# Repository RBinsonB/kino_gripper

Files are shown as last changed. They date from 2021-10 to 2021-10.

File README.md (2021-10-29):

# Kino Gripper
3D printed Kino gripper repository/ROS package.

Kino, from the greek κίνημα kinema ("movement, motion"), is an adaptative gripper using a [Dynamixel AX-12A servomotor](https://emanual.robotis.com/docs/en/dxl/ax/ax-12a/) as actuator. It leverages the abilies of the smart servomotor: compliance, possibility to set torque, velocity... Communication with the servomotor is handled with an integrated [USB2AX](http://www.xevelabs.com/doku.php?id=product:usb2ax:usb2ax). Power is provided by a DC-DC buck converter.

The gripper is designed to be mounted on a [HEBI Robotics Arm](https://www.hebirobotics.com/robot-arms) but can easily be modified to be mounted on other arms.

[Assembly instructions can be found here](/resources/documentation/kino_gripper_assembly.md).

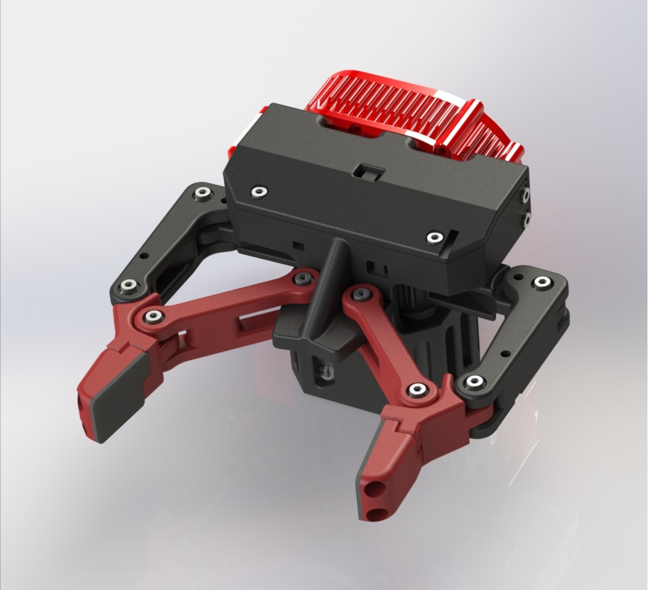
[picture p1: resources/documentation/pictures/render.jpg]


## Features

### Gripper mount
The gripper is designed to be mounted on a HEBI Robotics arm.



Screw the base attachement part to the output shaft of the HEBI actuator.



Connect with the main part of the gripper.



Slide the main part of the gripper, being careful not to damage the USB connector. Screw the main part in place

### Compliance
Torque and position compliance is provided by the servomotor. The compliance values can be set according to the [Dynamixel AX-12A documentation](https://emanual.robotis.com/docs/en/dxl/ax/ax-12a/#compliance-margin-26-27).

### Adaptive grip
Thanks to the spring on each finger, the gripper can fold to encircle small objects. The spring can be changed to allow for easier/harder finger deformation.

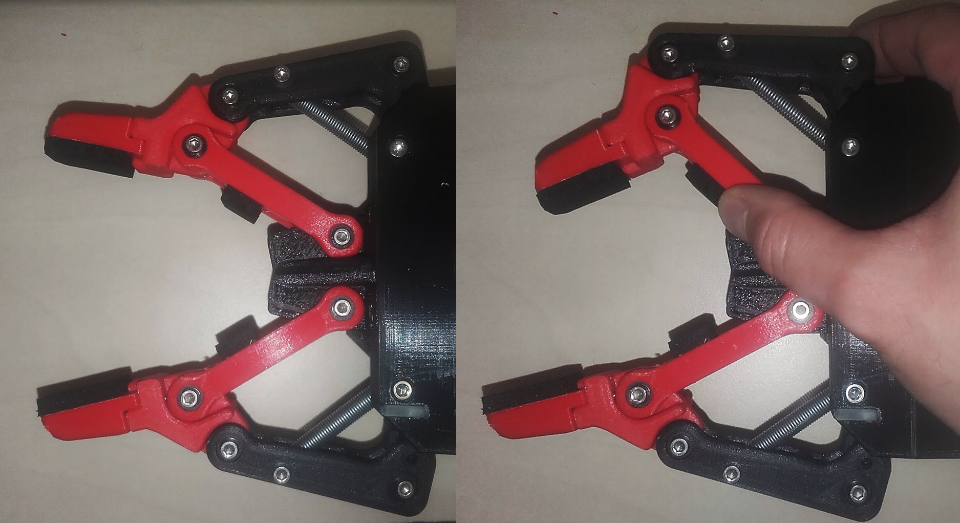
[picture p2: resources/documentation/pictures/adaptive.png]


### Changeable finger tips
Finger tips can be change by simply unscrewing/screwing.

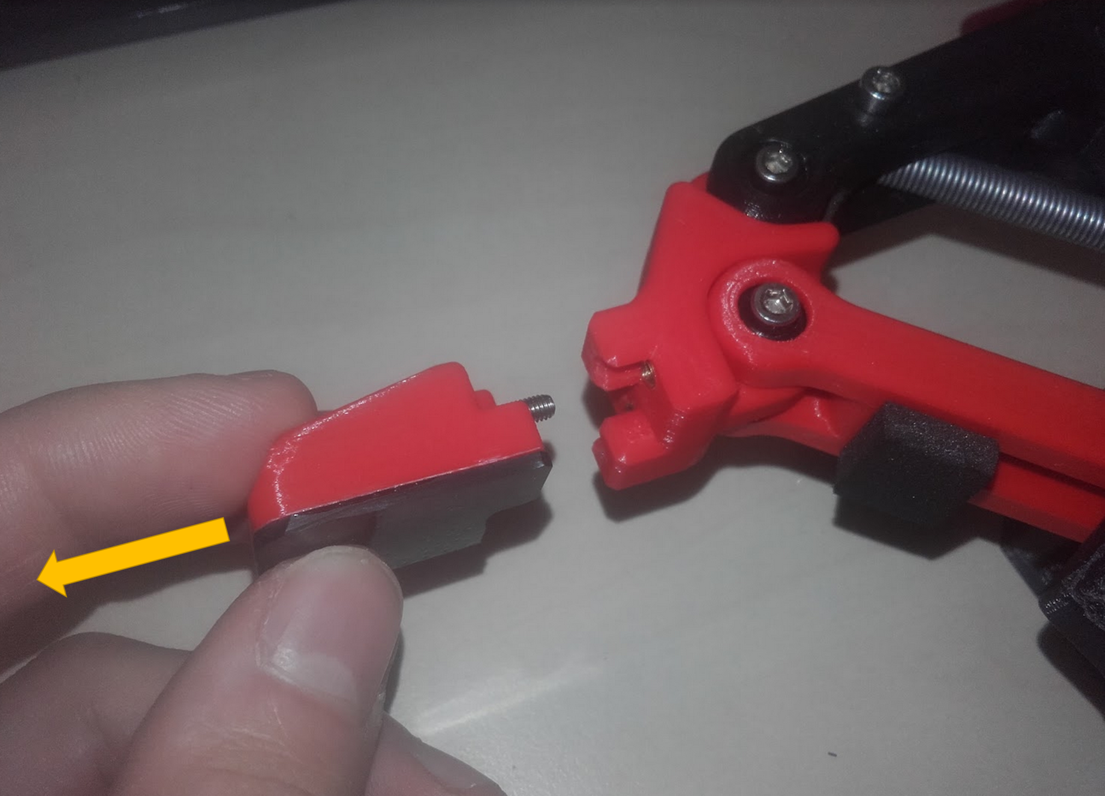
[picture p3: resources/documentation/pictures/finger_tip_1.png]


Three finger tip types are provided, but more can easily be designed:
* Default, with zig-zag pattern
* Thin pads, to be printed and completed by gluing a thin rubber pad
* Thick pads, to be printed and completed by gluing a thick foam pad

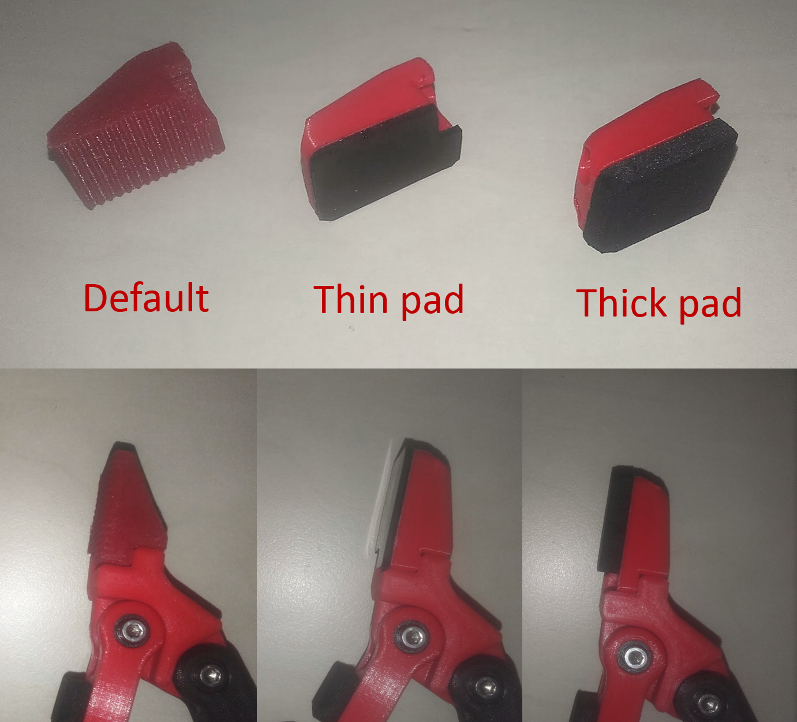
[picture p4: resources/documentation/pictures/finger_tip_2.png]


## Installation
The gripper package can be used as a ROS or C++ package.

### Dependencies
- [Robot Operating System (ROS)](http://wiki.ros.org)
- [Dynamixel SDK](https://emanual.robotis.com/docs/en/software/dynamixel/dynamixel_sdk/download/). Either through ROS package or direct install.

### Building
To build the package, clone the current repository in your catkin workspace and build it.
```
cd catkin_ws/src
git clone https://github.com/RBinsonB/kino_gripper.git
```
Build your workspace with either *catkin_make* or *catkin build*
```
cd ...
catkin_make
```

## Usage
### ROS Node
The gripper ROS node can be launched using the following command. Don't forget to set the appropriate port, device ID and baudrate parameters beforehand.
```
rosrun kino_gripper kino_gripper_node
```

#### Subscribed Topics
- `gripper_cmd` ([control_msgs/GripperCommand](http://docs.ros.org/en/melodic/api/control_msgs/html/msg/GripperCommand.html))

    Gripper command message. The position field is commanded distance between the fingers. Torque command is not taken into account and the default servomotor torque will be used.

#### Parameters
- `~port` (string, default: "/dev/ttyACM0")

    Servomotor port. For more information check about USB2AX and AX-12A Dynamixel servomotor.
    
- `~baudrate` (int, default: 1000000)

    Servomotor baudrate in bps. For more information check about USB2AX and AX-12A Dynamixel servomotor.
    
- `~device_id` (uint8_t, default: 1)

    Servomotor ID. For more information check about AX-12A Dynamixel servomotor.
    
### C++
The gripper library can be used independently of ROS. To do so, include the appropriate header in your file.
```cpp
#include <kino_gripper.h>

```

To use the gripper, you can create a gripper object using:
```cpp
KinoGripper(int device_id, char const* device_name, int baudrate)
```
The gripper can then be closed or opened using the Close() and Open() functions.
Example:
```cpp
KinoGripper gripper(1, "/dev/ttyACM0", 1000000);

gripper.Close(40.0);              // Close fingers to 40mm
while (!gripper.IsClosed()){ };   // Wait for gripper to finish
gripper.Close(0.0);               // Close fingers to 0mm
while (!gripper.IsClosed()){ };
gripper.Open();                   // Open gripper completely
while (!gripper.IsClosed()){ };
```

#### API
##### Public Member Functions
```cpp
KinoGripper(int device_id, char const* device_name, int baudrate)
  Gripper object constructor.
  Parameters : 
      device_id Dynamixel servomotor device ID
      device_name Dynamixel servomotor port
      baudrate Dynamixel servomotor baudrate in bps
```
```cpp
void InitGripper()
  Initializes the gripper servomotor and build lookup table for position command
```
```cpp
bool Close(float distance)
  Close the gripper to the given distance (between fingers)
  Parameters : 
      distance Distance between fingers in mm
  Returns :
      True if command sent successfully to servomotor
```
```cpp
bool Open()
  Open the gripper fully by sending maximum angle command (can be set SetMinMaxAngle())
  Returns :
      True if command sent successfully to servomotor
```
```cpp
bool IsClosed()
  Check if the gripper is closed at the value commanded via Close(), uses an inner hardcoded threshold.
  Returns :
      True if gripper is closed to the last commanded value
```
```cpp
bool IsMoving()
  Check if the gripper is moving.
  Returns :
      True if gripper is currently in motion
```
```cpp
bool SetSpeed(uint16_t speed)
  Set servomotor rotation speed
  Parameters : 
      speed Servomotor rotation speed in rev/min
  Returns :
      True if operation is successful
```
```cpp
bool SetMinMaxAngle(uint16_t min_angle, uint16_t max_angle)
  Set servomotor minimum and maximum angles
  Parameters : 
      min_angle Minimum servomotor angle in steps
      max_angle Maximum servomotor angle in steps
  Returns :
      True if operation is successful
```
```cpp
bool SetCompliance(uint8_t cw_margin, uint8_t ccw_margin, uint8_t cw_slope, uint8_t ccw_slope, uint16_t punch)
  Set servomotor compliance parameters. For more information, check Dynamixel AX-12A control table for more details.
  Parameters : 
      cw_margin Clockwise compliance margin in deg 
      ccw_margin Counter-clockwise compliance margin in deg
      cw_slope Clockwise compliance slope
      ccw_slope Counter-clockwise compliance slope
      punch Punch
  Returns :
      True if operation is successful
```
## License
All rights reserved

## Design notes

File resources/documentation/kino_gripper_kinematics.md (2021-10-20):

# Gripper Kinematics

## Forward Kinematics
The gripper dimensions (right finger) are simplified and detailed below.

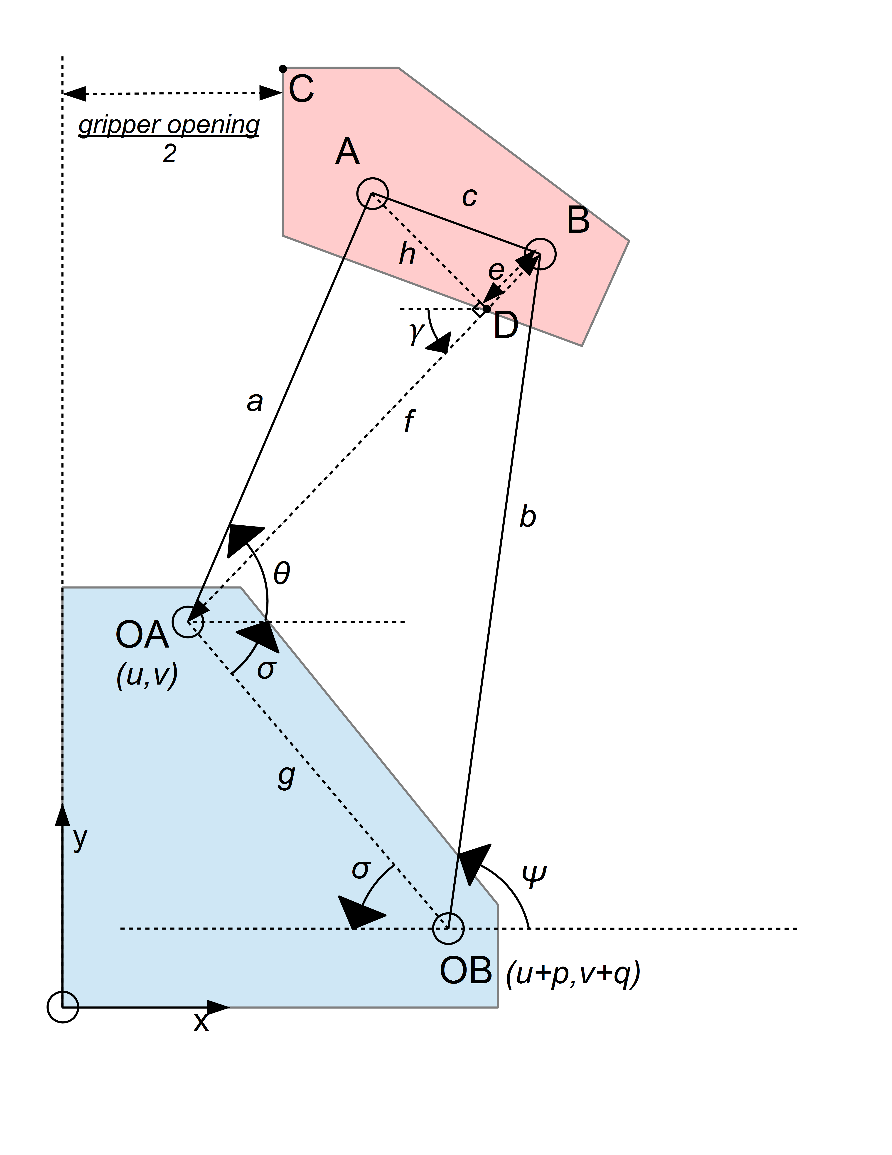
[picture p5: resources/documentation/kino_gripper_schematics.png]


The following equations can be deducted:
* Ax = u + a×cos(θ)
* c² = (Ax-Bx)² + (Ay-By)²
* f² = (u-Bx)² + (v-By)²
* By = v + q + b×sin(ψ)
* By = u + p + b×cos(ψ)
* g = (p²+q²)½
* c² = e² + h²
* Cx = u - r
* Cy = v + s
* cos(γ+σ) = (g²+f²-b²)/2gf
* Dx = u + (f-e)×cos(γ)
* Dy = v + (f-e)×sin(γ)
* Ay = Dy + h×sin((π/2)-γ)
	 = Dy + h×cos(-γ)
* γ = acos(g²+f²-b²/2gf) - σ
* e = (a²+f²+c²)/2gf

from those:
* σ = asin(q/g) = acos(p/g)

* cos(π-σ-ψ) = (g² + b² - f²) / 2gb 
	<=> f² = -2gb×cos(π-σ-ψ) + g² + b²

* h = (c² - e²)½

* c² - f² = Ax² - 2AxBx + Ay² - 2AyBy - u² + 2uBx - v² + 2vBy
	<=> Ax² - (2Bx)×Ax + (Ay² - 2AyBy - u² + 2uBx - v² + 2vBy - c² + f²) = 0 ; and defining z = (Ay² - 2AyBy - u² + 2uBx - v² + 2vBy - c² + f²)
	<=> Ax = (2Bx ± (4Bx² - 4z)½) / 2 = Bx ± (Bx²-z)½
	<=> since Ax < Bx and (...)½ > 0 => Ax = Bx - (Bx²-z)½

* Cx = Ax - r
* Opening distance = Cx × 2

The distance can therefor be obtained from the servo angle ψ.

## Inverse Kinatics
The inverse kinematics solution is obtain using a lookup table. The table is populated using the forward kinematics for every possible servo angle command.

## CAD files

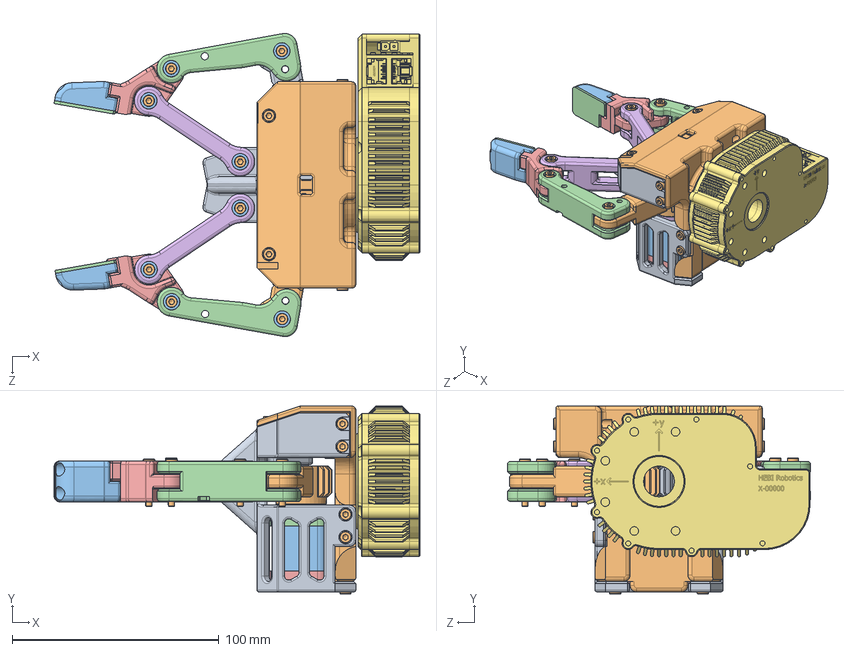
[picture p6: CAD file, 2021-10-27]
resources/CAD/kino_gripper.SLDASM
177.2 x 91.0 x 146.8 mm
base
base_attachement
AX-12A-01
AX-12A-02
AX-12A-03
AX-12A-04
SetScrew x 4
pan head cross recess screw_iso
right-finger-gear
tunable-gear
radial ball bearing_68_iso x 18
outer_finger x 2
end_finger x 2
central_finger x 2
X5-1
step_down_converter
uab2ax
socket head cap screw_iso x 20
finger_tip_pad x 2

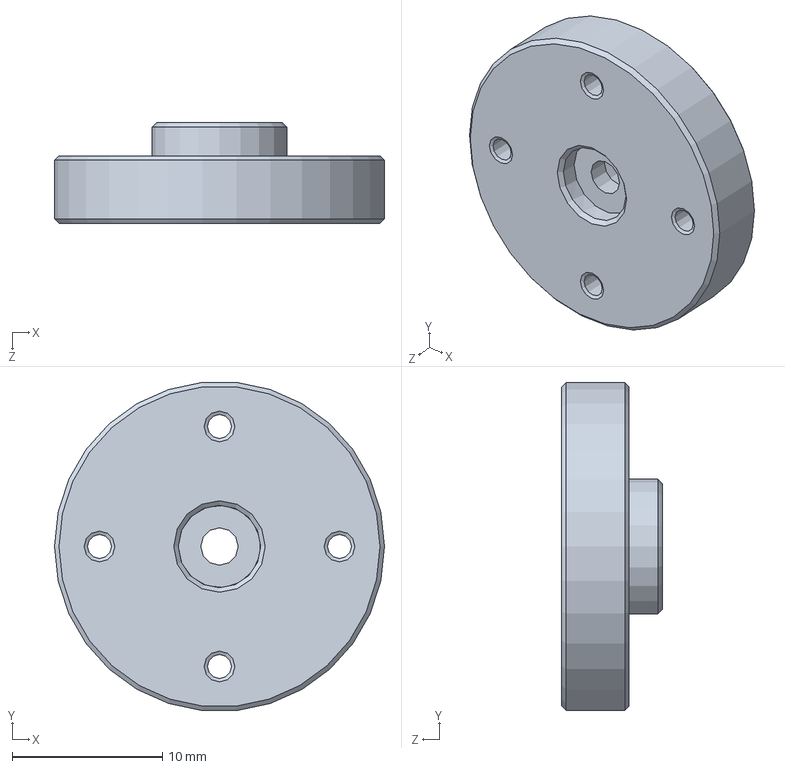
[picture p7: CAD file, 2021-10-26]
resources/CAD/dynamixel_AX-12A/AX-12A-04.SLDPRT
22.0 x 21.9 x 6.70 mm

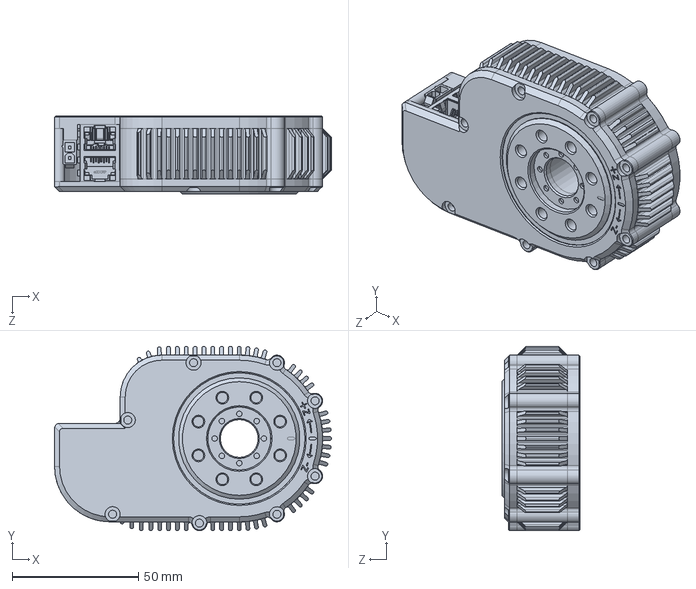
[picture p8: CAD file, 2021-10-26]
resources/CAD/hebi_actuators/X5/X5-9.SLDPRT
109.6 x 73.0 x 31.1 mm

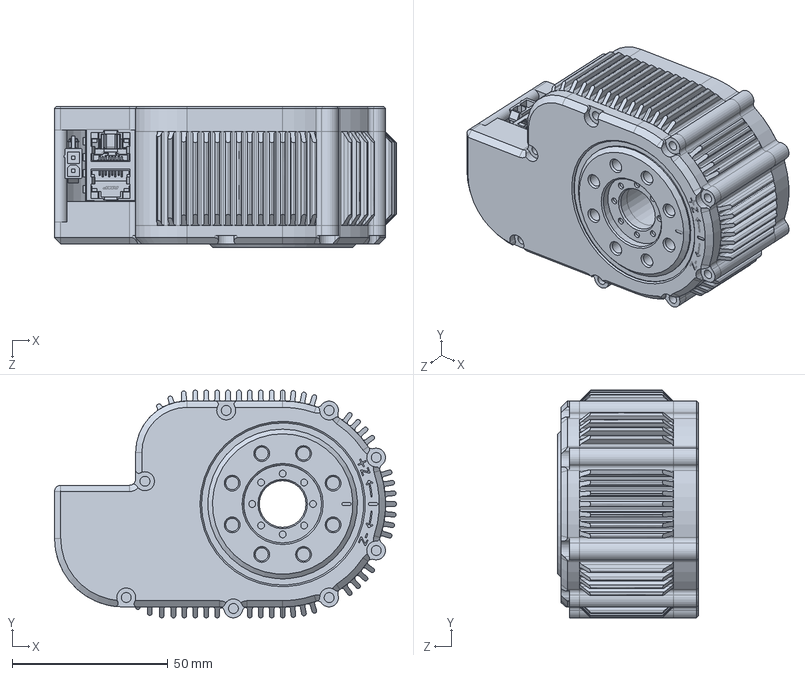
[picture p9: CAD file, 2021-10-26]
resources/CAD/hebi_actuators/X8/X8-9.SLDPRT
109.6 x 73.0 x 45.0 mm

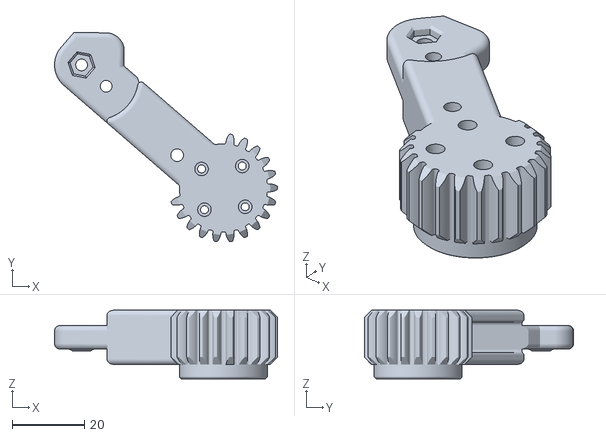
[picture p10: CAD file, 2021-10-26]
resources/STL/left_finger_gear.STL
61.8 x 58.0 x 19.0

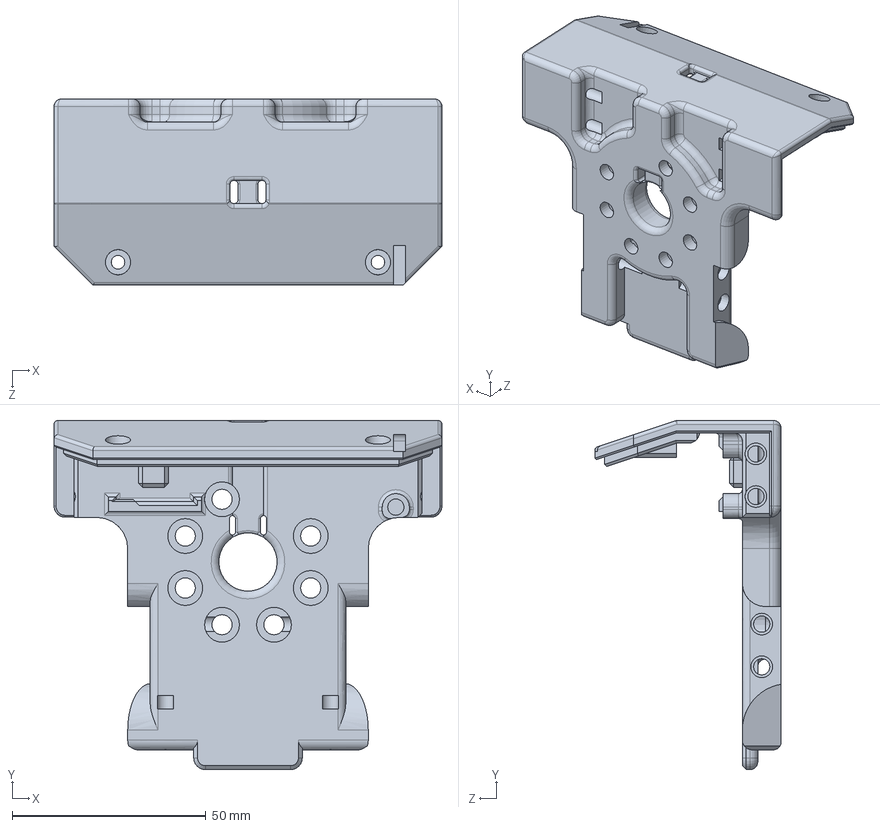
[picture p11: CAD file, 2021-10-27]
resources/CAD/base_attachement.SLDPRT
100.0 x 90.0 x 48.0 mm

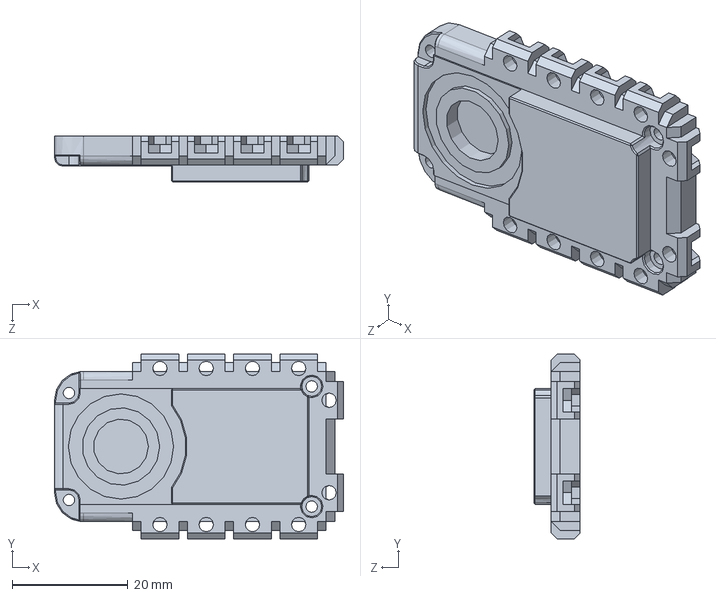
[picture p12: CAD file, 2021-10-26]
resources/CAD/dynamixel_AX-12A/AX-12A-02.SLDPRT
50.0 x 32.0 x 8.00 mm

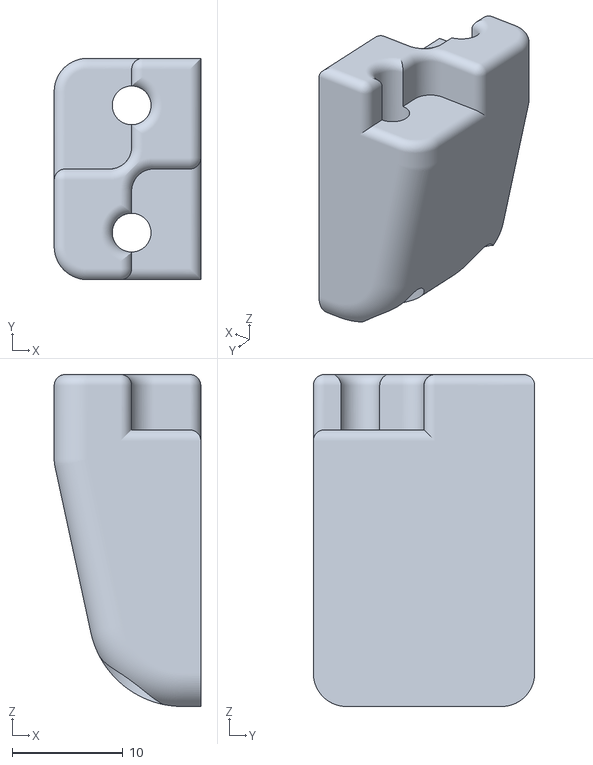
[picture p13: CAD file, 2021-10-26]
resources/STL/finger_tip_pad_left.STL
13.2 x 20.0 x 30.0

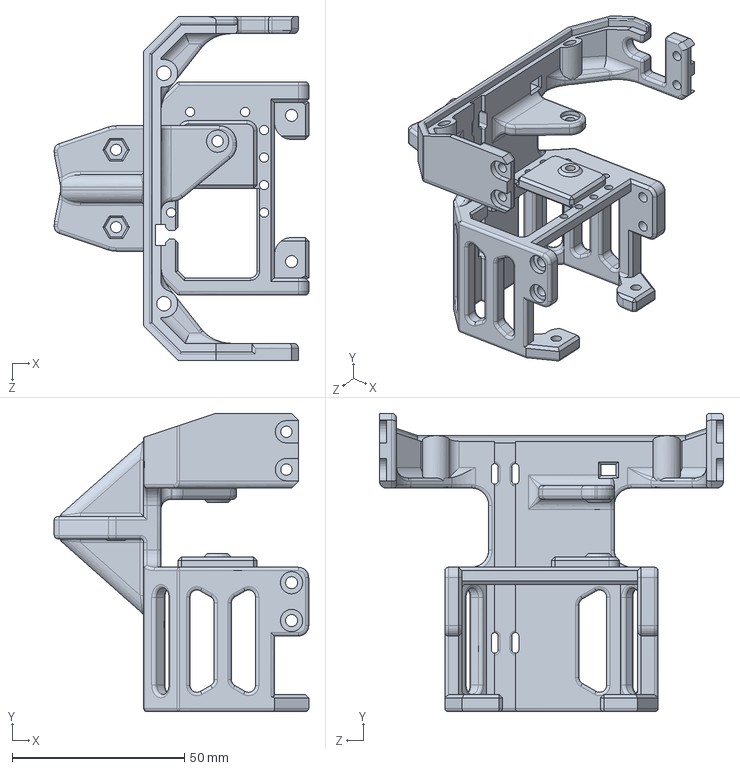
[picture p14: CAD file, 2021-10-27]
resources/CAD/base.SLDPRT
74.0 x 86.8 x 100.0 mm

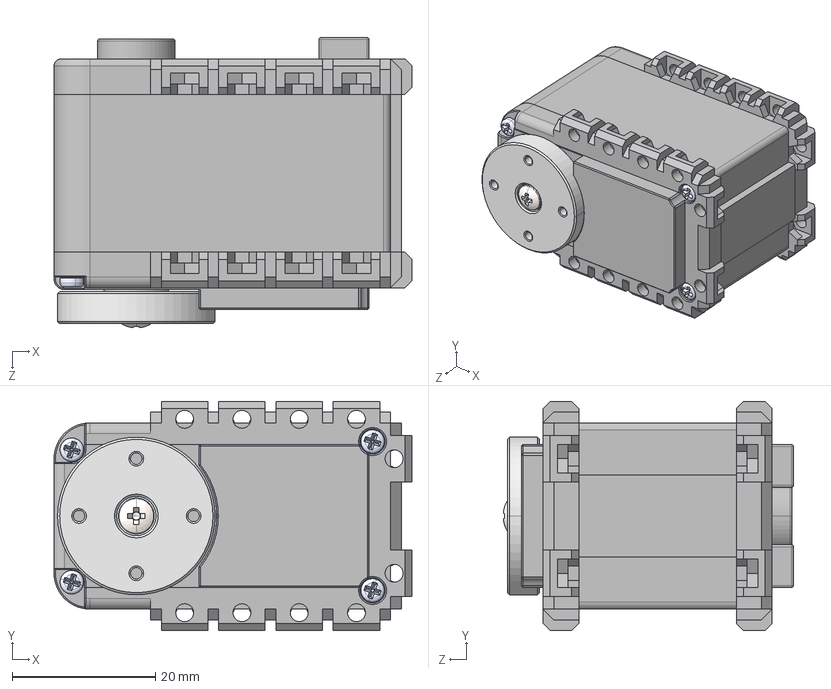
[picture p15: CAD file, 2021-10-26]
resources/CAD/dynamixel_AX-12A/AX-12A.STEP
50.0 x 32.0 x 40.5 mm
AX-12A-01
AX-12A-02
AX-12A-03
AX-12A-04
SetScrew x 4
pan head cross recess screw_iso_ISO 7045 - M2.5 x 8 - Z --- 8C

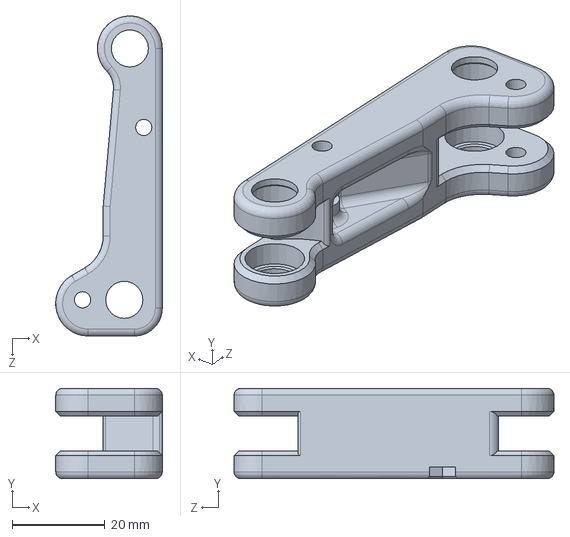
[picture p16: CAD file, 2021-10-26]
resources/CAD/outer_finger.SLDPRT
23.0 x 19.5 x 69.0 mm

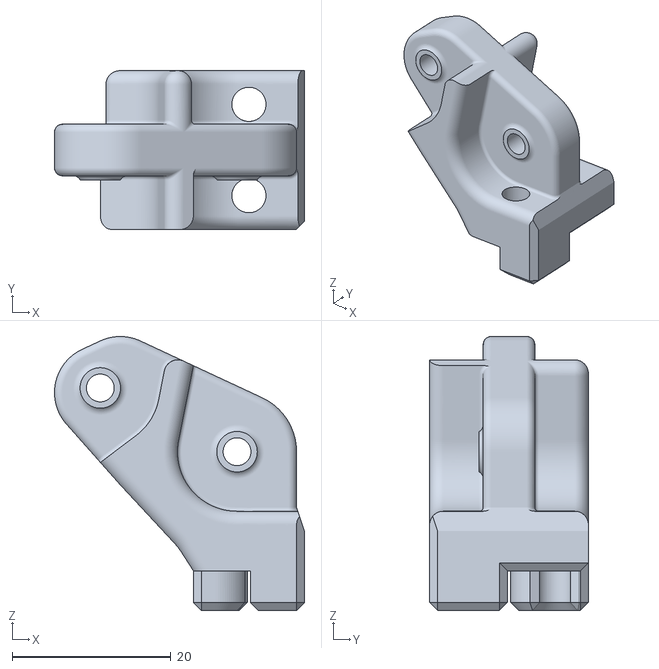
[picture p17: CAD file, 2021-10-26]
resources/STL/end_finger_left.STL
31.5 x 20.0 x 34.5

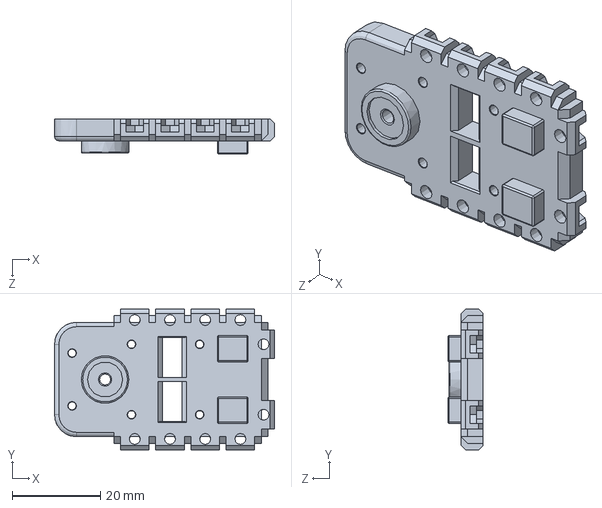
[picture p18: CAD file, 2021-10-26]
resources/CAD/dynamixel_AX-12A/AX-12A-03.SLDPRT
50.0 x 32.0 x 8.00 mm

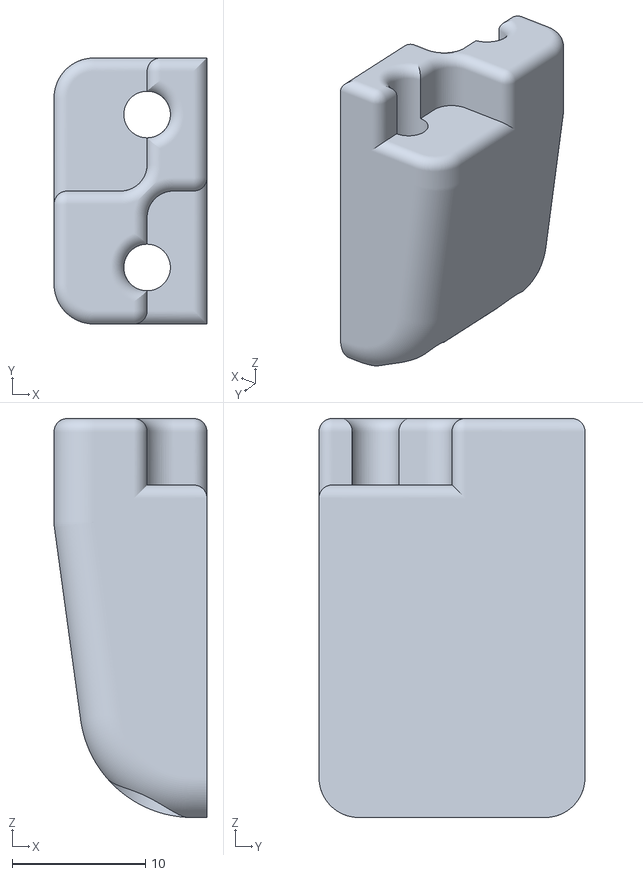
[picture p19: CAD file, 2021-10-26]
resources/STL/finger_tip_thick_pad_left.STL
11.5 x 20.0 x 30.0

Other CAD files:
resources/CAD/hebi_actuators/X5/X5-1.SLDPRT
resources/CAD/hebi_actuators/X8/X8-16.SLDPRT
resources/STL/finger_tip_pad_right.STL
resources/CAD/tunable-gear.SLDPRT
resources/CAD/central_finger.SLDPRT
resources/CAD/central_finger_pad.SLDPRT
resources/CAD/central_finger_v2.SLDPRT
resources/CAD/dynamixel_AX-12A/AX-12A-01.SLDPRT
resources/CAD/dynamixel_AX-12A/AX-12A.SLDASM
resources/CAD/dynamixel_AX-12A/SetScrew.SLDPRT
resources/CAD/end_finger.SLDPRT
resources/CAD/end_finger_v2.SLDPRT
resources/CAD/finger_tip.SLDPRT
resources/CAD/finger_tip_pad.SLDPRT
resources/CAD/outer_finger_v2.SLDPRT
resources/CAD/pad.SLDPRT
resources/CAD/right-finger-gear.SLDPRT
resources/CAD/spur gear_iso.sldprt
resources/CAD/step_down_converter.SLDPRT
resources/CAD/uab2ax.SLDPRT
resources/STL/base_attachement.STL
resources/STL/central_finger.STL
resources/STL/central_finger_left.STL
resources/STL/central_finger_pad.STL
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

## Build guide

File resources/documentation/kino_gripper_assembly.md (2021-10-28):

# Assembly instructions
## Necessary parts

The following parts are required to assemble the gripper.

### Printed parts
* (1x) [Base](/resources/STL/base.STL)
* (1x) [Base attachement](/resources/STL/base_attachement.STL)
* (1x) [Gear finger right](/resources/STL/right_finger_gear.STL)
* (1x) [Gear finger left](/resources/STL/left_finger_gear.STL)
* (1x) [Outer finger right](/resources/STL/outer_finger.STL)
* (1x) [Outer finger left](/resources/STL/outer_finger_left.STL)
* (1x) [Central finger right](/resources/STL/central_finger.STL)
* (1x) [Central finger left](/resources/STL/central_finger_left.STL)
* (1x) [End finger right](/resources/STL/end_finger.STL)
* (1x) [End finger left](/resources/STL/end_finger_left.STL)
* (1x) finger tips, multiple options possible:
  * Without pads:
    * (1x) [finger tip left](/resources/STL/finger_tip_left.STL)
    * (1x) [finger tip right](/resources/STL/finger_tip.STL)
  * With thin pads:
    * (1x) [finger tip pads left](/resources/STL/finger_tip_pad_left.STL)
    * (1x) [finger tip pads right](/resources/STL/finger_tip_pad_right.STL)
  * With thick pads:
    * (1x) [finger tip thick pads left](/resources/STL/finger_tip_thick_pad_left.STL)
    * (1x) [finger tip thick pads right](/resources/STL/finger_tip_thick_pad.STL)

### Electronics
* (1x) [Dynamixel AX-12A Servomotor](https://emanual.robotis.com/docs/en/dxl/ax/ax-12a/)
* (1x) [USB2AX](http://www.xevelabs.com/doku.php?id=product:usb2ax:usb2ax)
* (1x) Voltage regulator (step-down) LM2596 boards. The boards are cheap and easily findable online, but they should have the following dimensions to fit within the case.

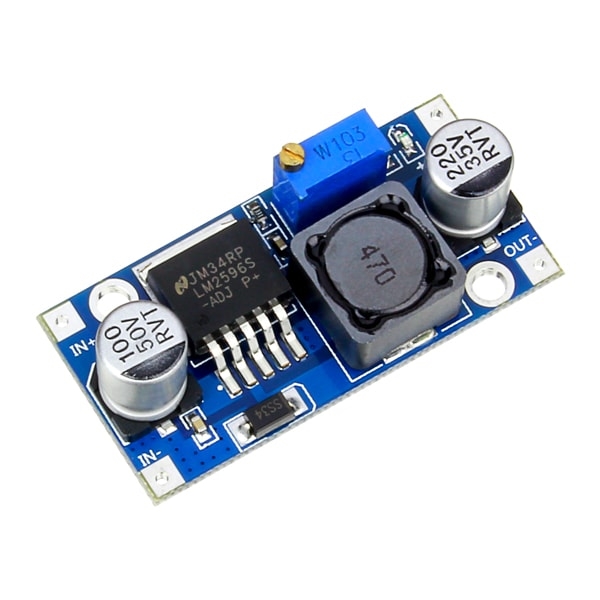
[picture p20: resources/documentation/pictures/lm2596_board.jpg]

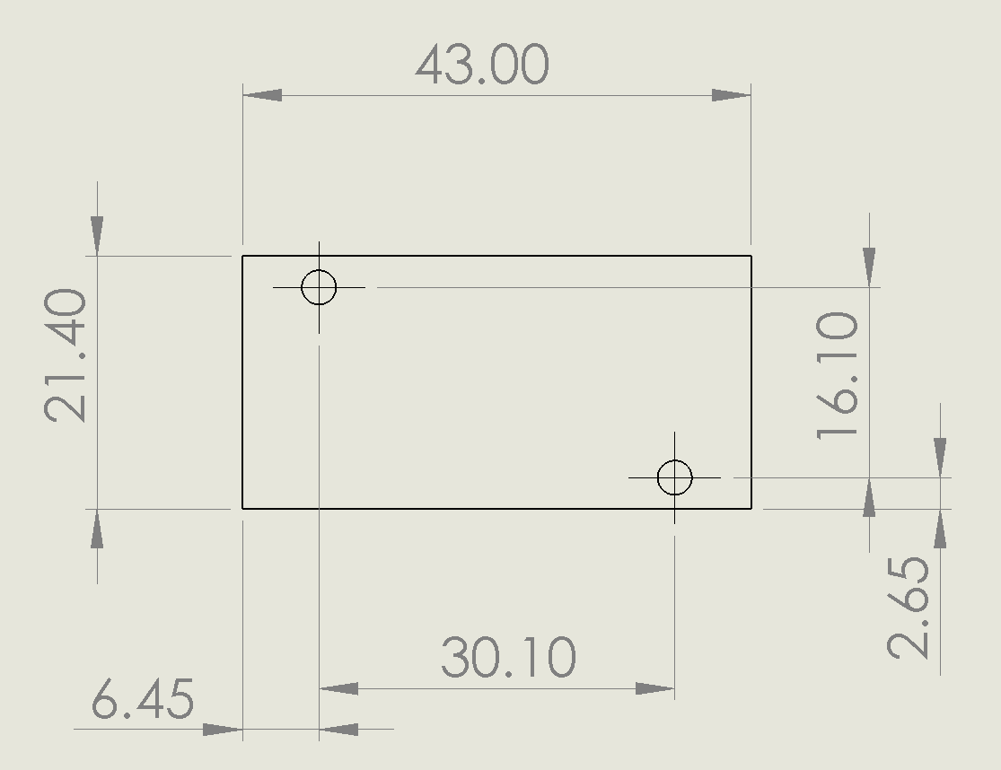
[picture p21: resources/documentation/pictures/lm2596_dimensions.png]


### Mechanical parts
* (18x) Ball bearing 10x4x3mm
* (2x) Extension spring (length max of 50mm at rest, diameter max of 8.5mm)
* (12x) M3 inserts (M4 outer diameter)
* (7x) M3 nuts
* (8x) (optionally self-locking) M3 nuts
* (12x) M3 x 16mm hex socket head screws
* (8x) M3 x 20mm hex socket head screws
* (2x) M3 x 5mm hex socket head screws
* (1x) M3 x 25mm countersunk head screw
* (7x) M5 x 8mm hex socket head screws (for attaching to the HEBI actuator)
* (6x) M2 x 10mm screws (for fastening servomotor)
* (6x) M2 nuts (for fastening servomotor)
* (4x) M2 x 5mm screws (for fastening on servomotor's ouptut shaft)
* (3x) Zip ties

### Connectors
* (1x) Molex minifit Jr. male housing (2x1) and its associated crimp terminals (for connecting with HEBI Robotics Arm power supply)
* (2x) Mini-SPOX 2.50mm female housing (3 pins) and its associated crimp terminals (for connecting with the Dynamixel AX-12A servomotor, check [Dynamixel servomotor documentation](https://emanual.robotis.com/docs/en/dxl/ax/ax-12a/#connector-information) for more information)
* (1x) male & female connector (and associated crimp terminals) with at least 3 pins, small enough to fit inside the gripper. Here, a 2x2 Molex Microfit is used.

### Printing the parts
#### PLA
Most parts were printed using Ultimaker black/red PLA and/or black tough PLA with PVA supports (dual-printcore printer). The PVA support material is disovable in water and allow for a high precision in the printed connector housings. It's probably possible to print the parts without the PVA support material, but that would require more post-processing to remove the supports.

The following printing parameters were used for all parts printed in PLA:

| Parameter | Value |
| --- | ----- |
| Layer height | 0.15mm |
| Infill | 50% |
| Infill pattern | cubic subdivision |
| Support material | PVA |
| Support pattern | triangles |
| Support overhang | 45% |

### Assembling everything

Add the inserts in the attachment part. Use a soldering iron is needed.

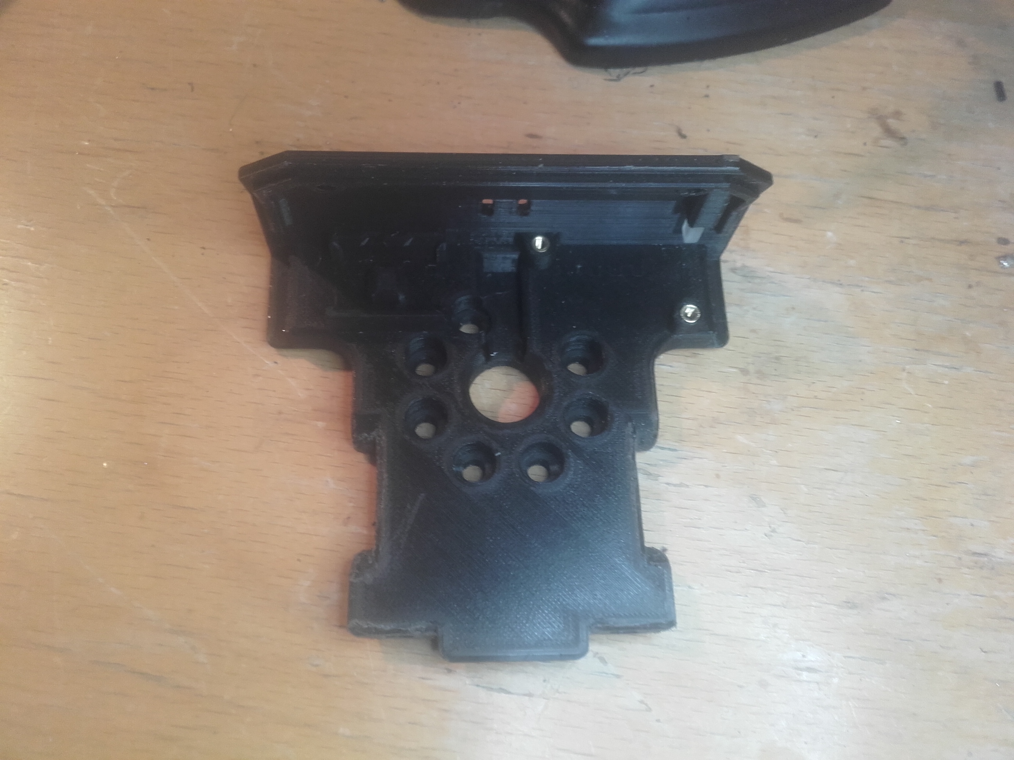
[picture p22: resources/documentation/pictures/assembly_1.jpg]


Clip in the USB2AX.

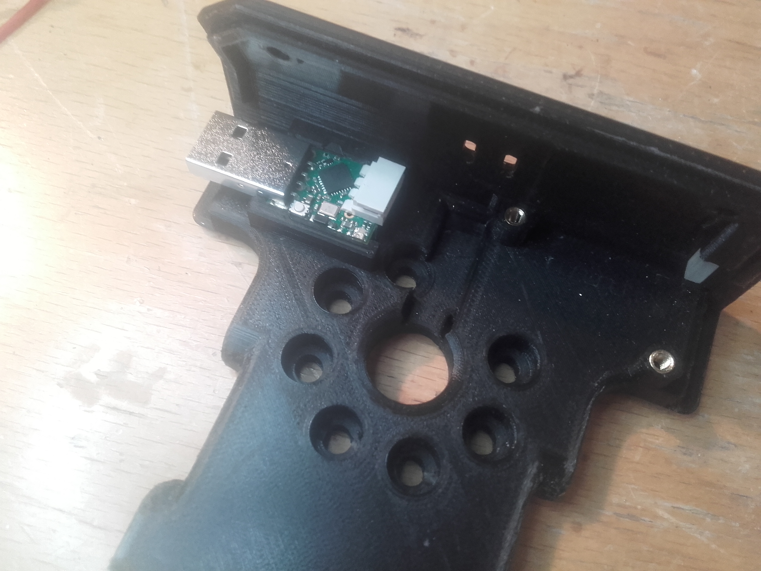
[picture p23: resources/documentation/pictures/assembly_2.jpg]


Solder the required wires on the DC power supply. It is also a good time to adjust the voltage output for the servomotor (between 9V and !"V, ideally 11.1V).

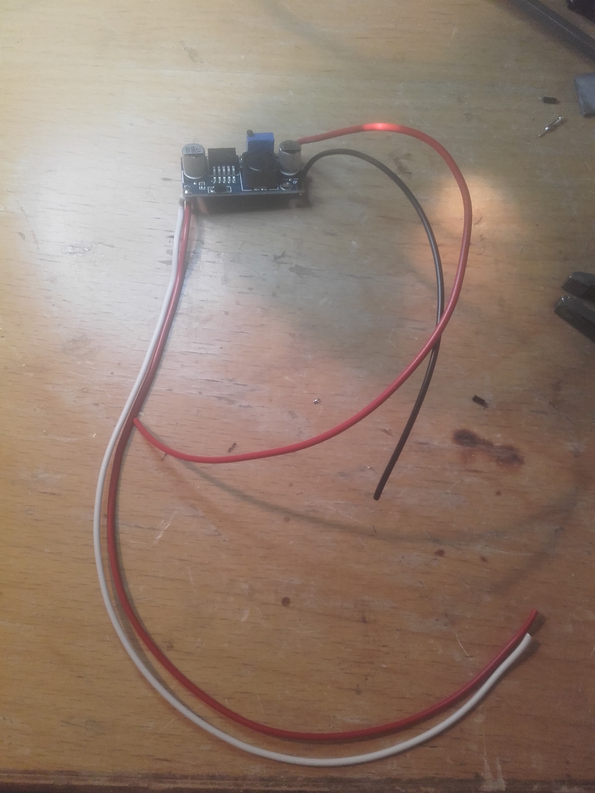
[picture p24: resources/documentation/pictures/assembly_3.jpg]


It can be then screwed in place using M3x5mm screws. On the other end on the input wires, crimp the minifit male housing connector, so that the gripper can be plugged to the HEBI Robotics power supply.

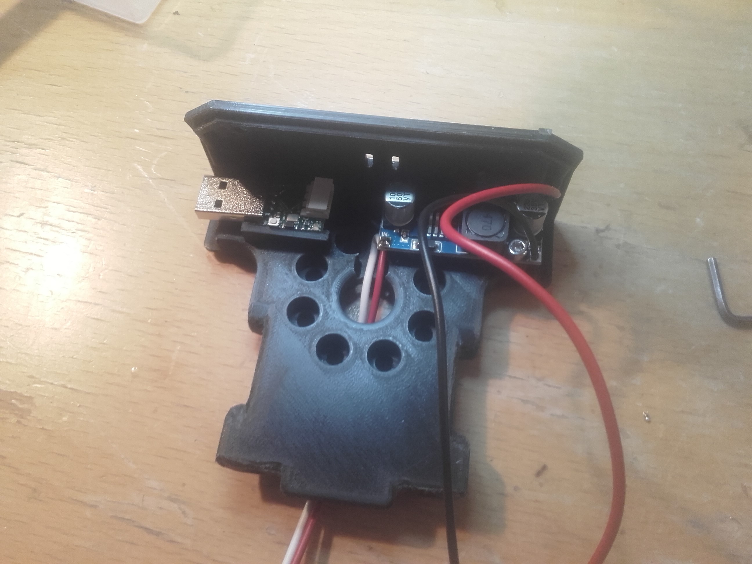
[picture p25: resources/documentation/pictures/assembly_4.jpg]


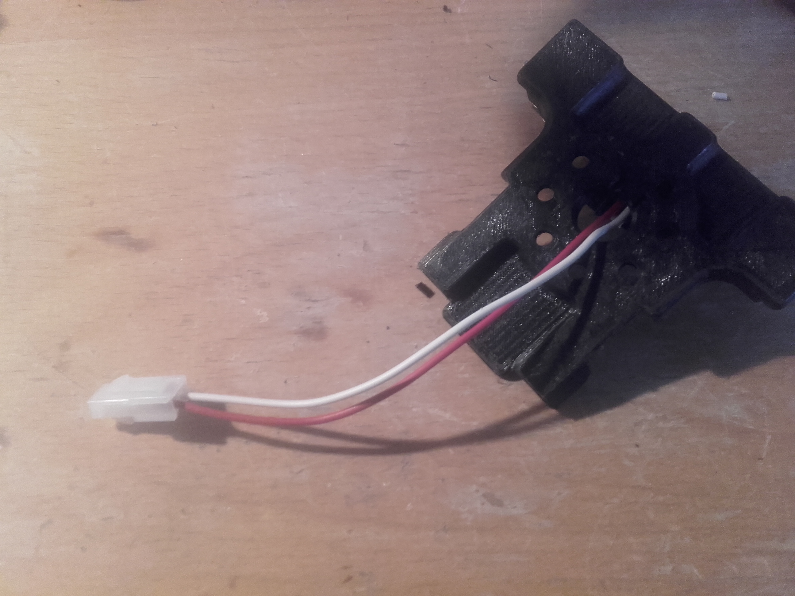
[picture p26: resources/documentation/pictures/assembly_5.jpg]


Prepare the output cable of the USB2AX by crimping a mini-SPOX connector. Only the two side wires should be connected, not the middle one, since power will be provided by the DC power supply.

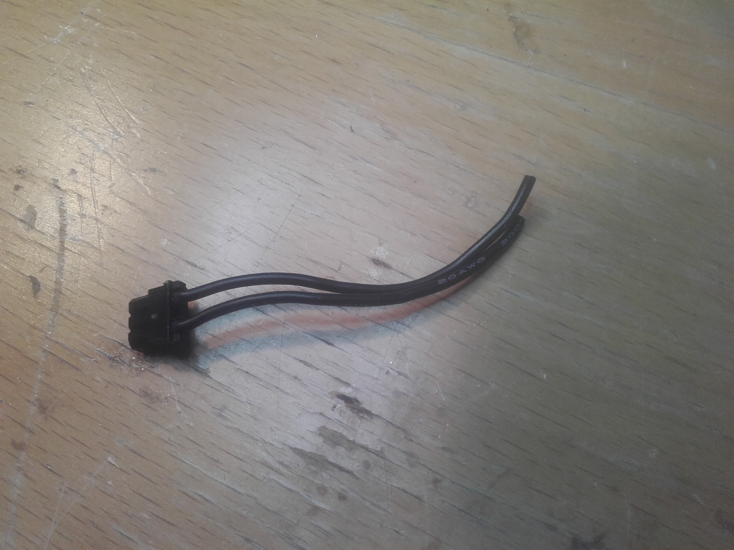
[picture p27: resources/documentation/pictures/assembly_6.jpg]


Connect the cable and ziptie it with the power output wires.

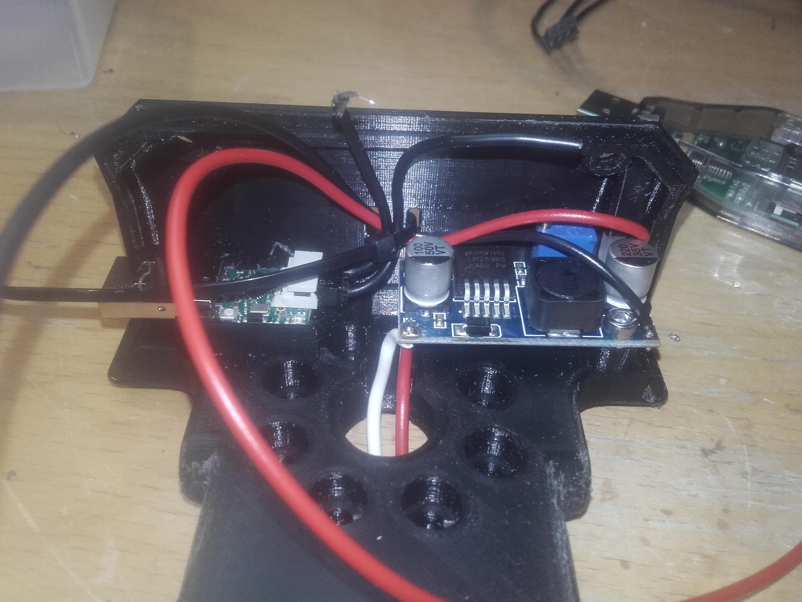
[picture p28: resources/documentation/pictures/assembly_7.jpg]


Respecting the connector pins, crimp the output power sypply ground and the USB2AX output ground together. Connect the ground, data output wire and power supply positive wire in a connector (here a Molex microfit).

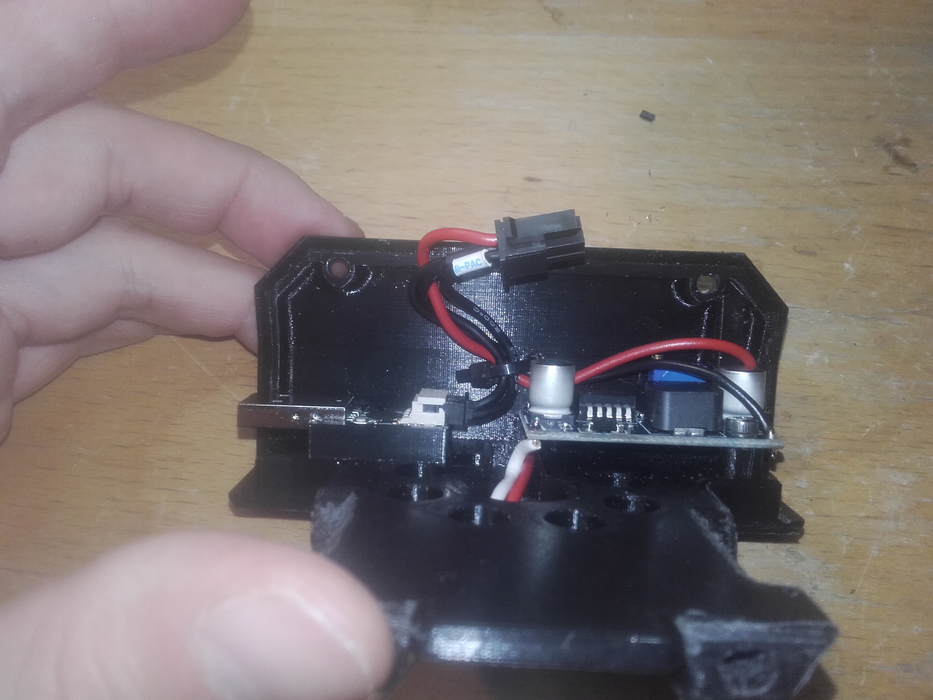
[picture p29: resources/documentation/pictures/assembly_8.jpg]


On the other main part, prepare a cable that will be connected to the servomotor. Crimp a mini-SPOX connector on one side and the complementary connector (here a Molex microfit), respecting the wiring of Dynamixel AX12-A servomotor. Fasten the cable against the part using zipties.

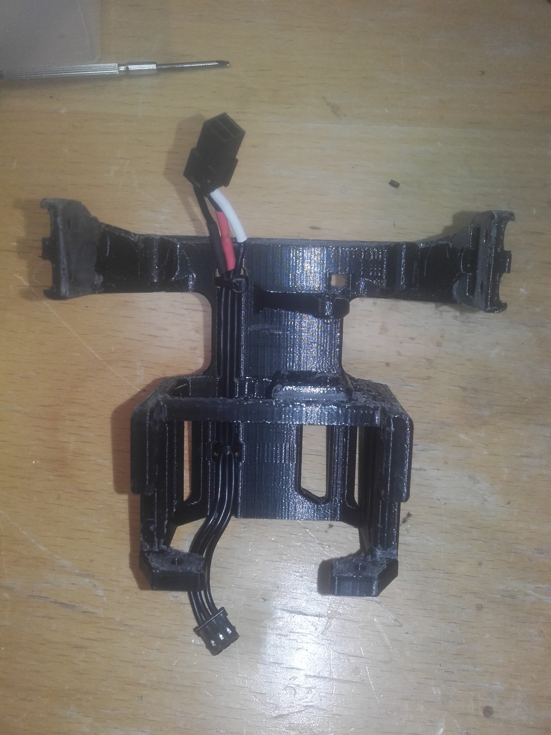
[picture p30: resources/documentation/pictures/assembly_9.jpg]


Insert the M3 nut under the part.

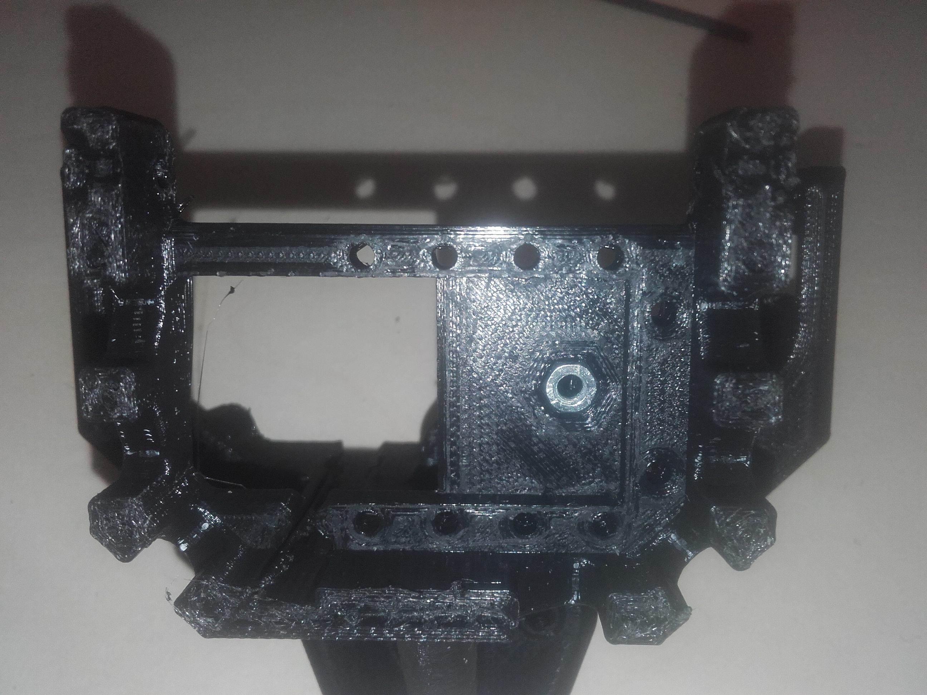
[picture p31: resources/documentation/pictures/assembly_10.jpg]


Put the servomotor in place, sliding it from under, and fasten it using M2x10mm screws.

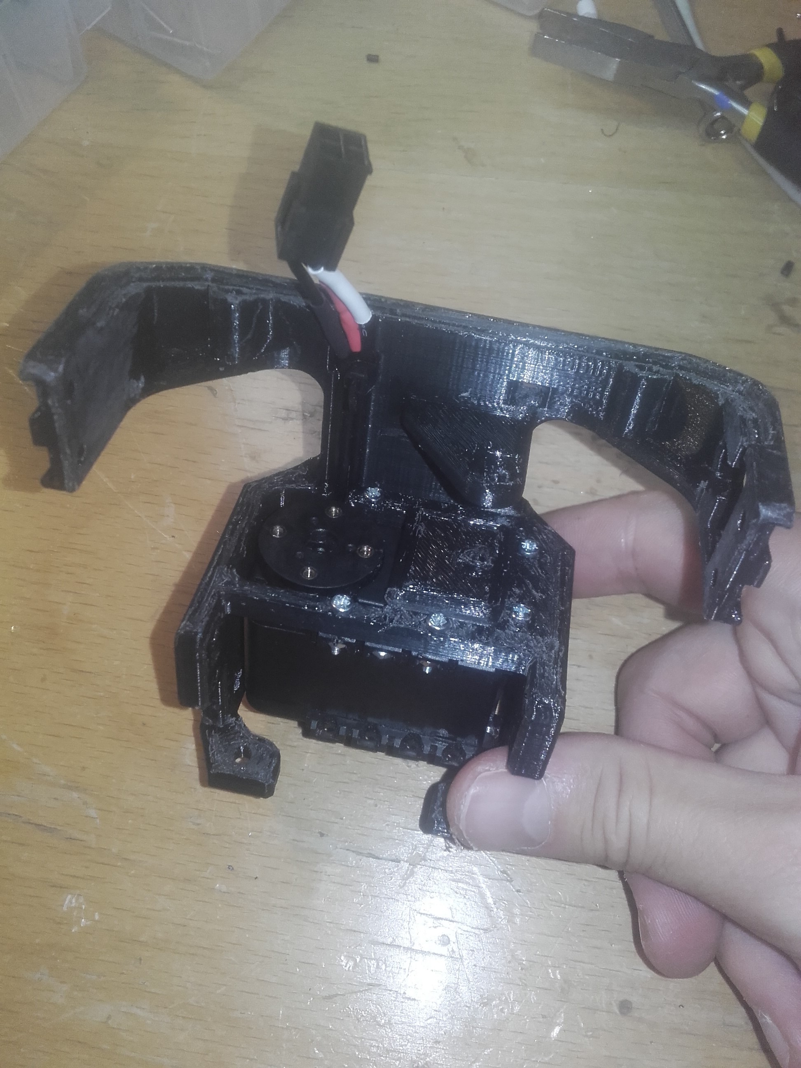
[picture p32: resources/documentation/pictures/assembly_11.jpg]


Prepare the right geared finger by mounting the 2 ball bearing on its axle, one on each side.

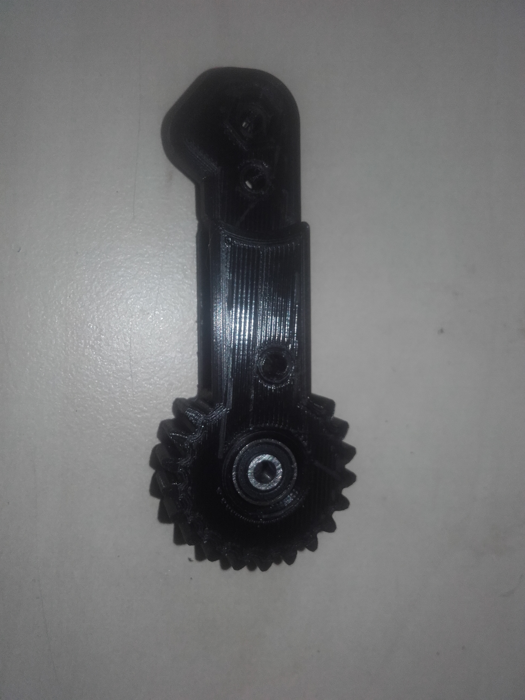
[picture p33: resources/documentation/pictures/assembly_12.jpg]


Slide the finger in place and fasten it on its axle using a M3x25mm countersunk head screw.

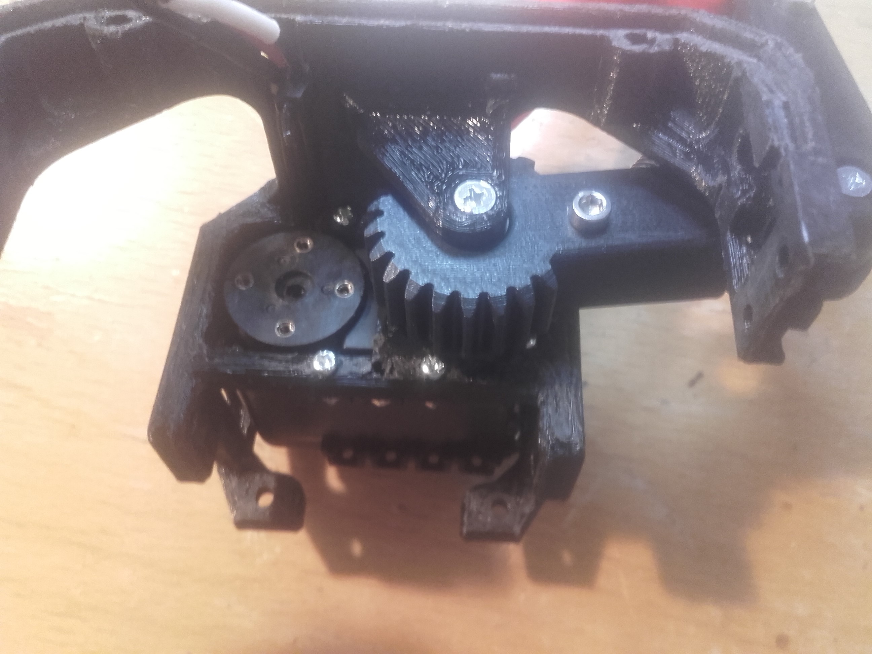
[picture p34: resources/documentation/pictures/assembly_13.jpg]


Put the servomotor to its 0deg position (512 in step command). This cam be done manually by turning the ouput shaft of the servo until the mark on the shaft aligns with the one on the servomotor body. The recommended and more reliable approach is to power the servomotor, plug to the USB, and use the [Dynamixel Wizard](https://emanual.robotis.com/docs/en/software/dynamixel/dynamixel_wizard2/) to command the servromotor to the 0deg (cmd 512) position.

Then screw the left geared finger on the servomotor with M2x5mm screws, making sure the left and right finger are aligned at the same angle.

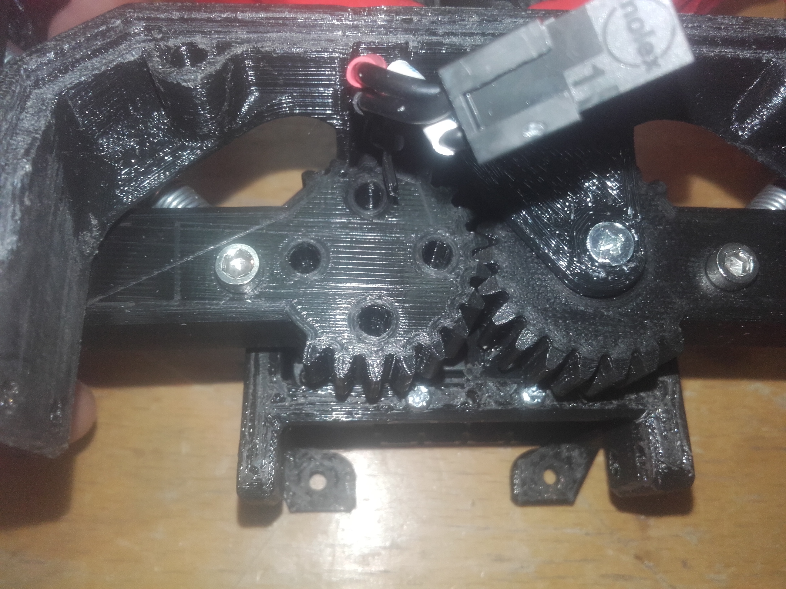
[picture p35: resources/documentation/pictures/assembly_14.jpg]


Screw the spring in place on both geared finger, using a nut on the other side.

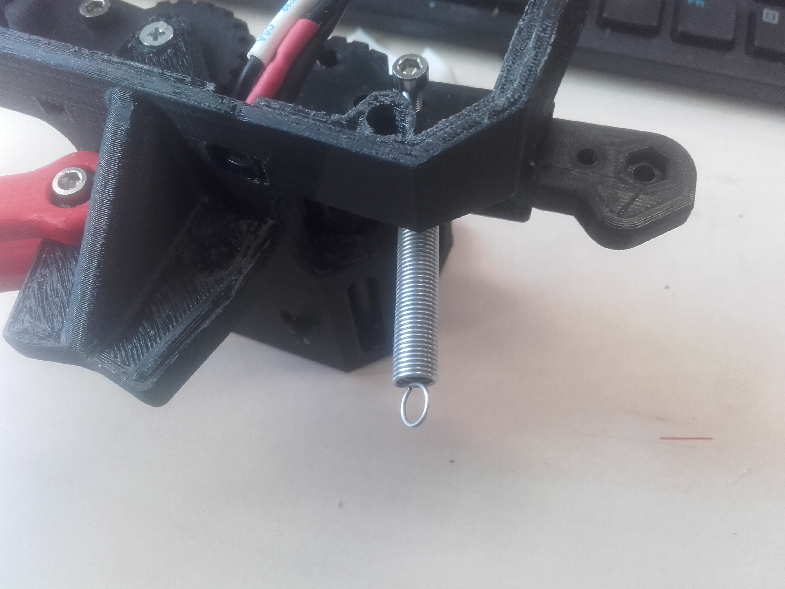
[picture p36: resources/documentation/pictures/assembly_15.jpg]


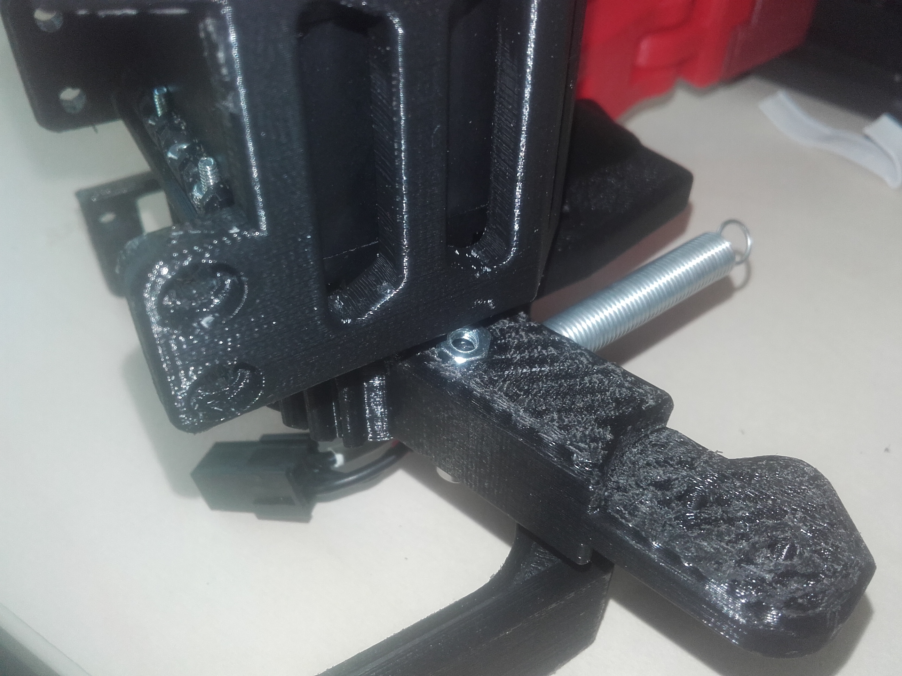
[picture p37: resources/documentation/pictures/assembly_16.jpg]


Add M3 inserts in the finger end parts, using a soldering iron if needed.

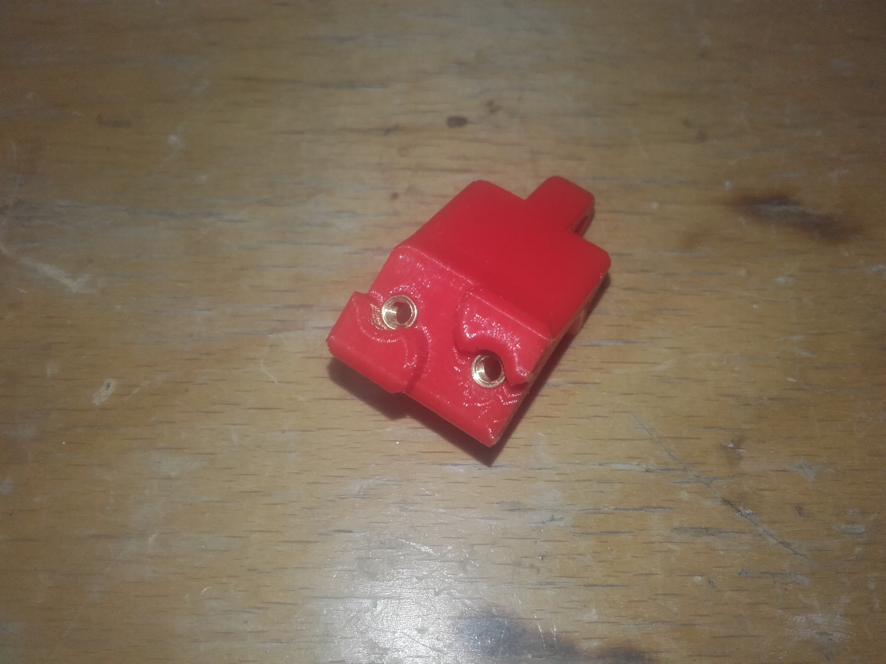
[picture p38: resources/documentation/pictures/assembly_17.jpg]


Assemble the rest of the fingers. For every pivot the method is the same. On the inner part, place a M3 nut. It might be needed to force it place but be careful if using a soldering iron, as it should not be pushed deeper than its housing.

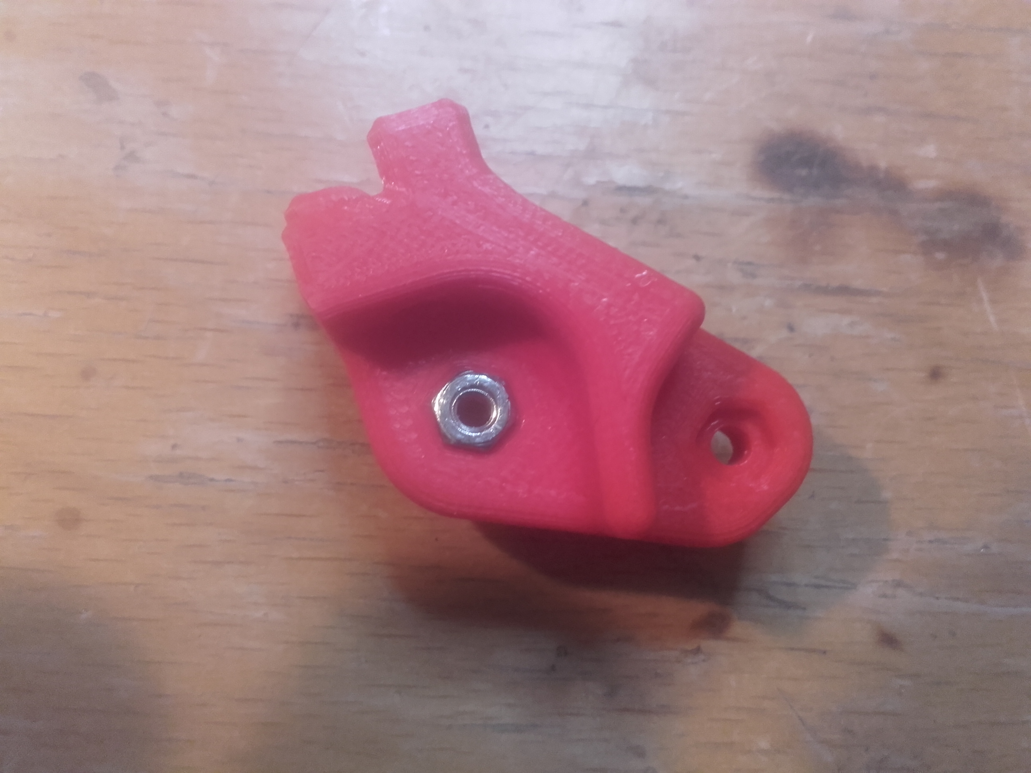
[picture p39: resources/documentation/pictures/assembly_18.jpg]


On the outer part, place a ball bearing on each side, from the interior. It might be need to push with a screwdriver or so to lock it in place.

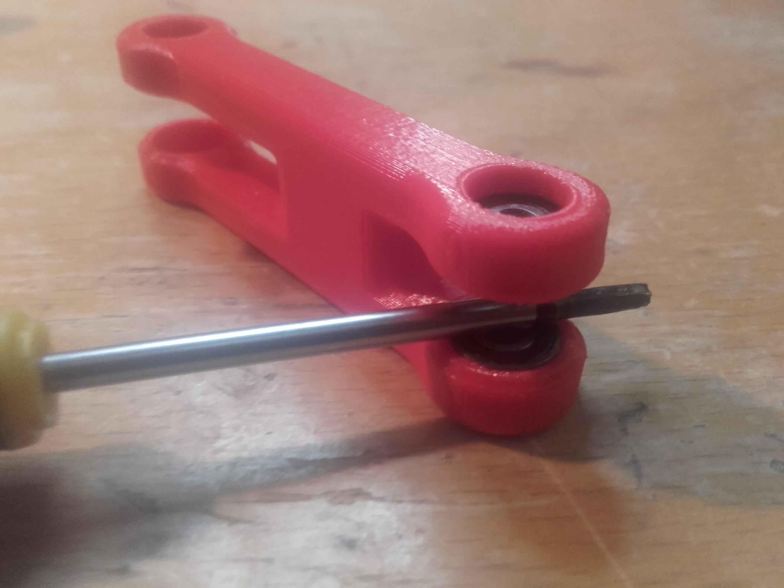
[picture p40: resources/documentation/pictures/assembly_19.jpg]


Slide the outer part on the inner one. It is normal if the assembly is tight and difficult to align.

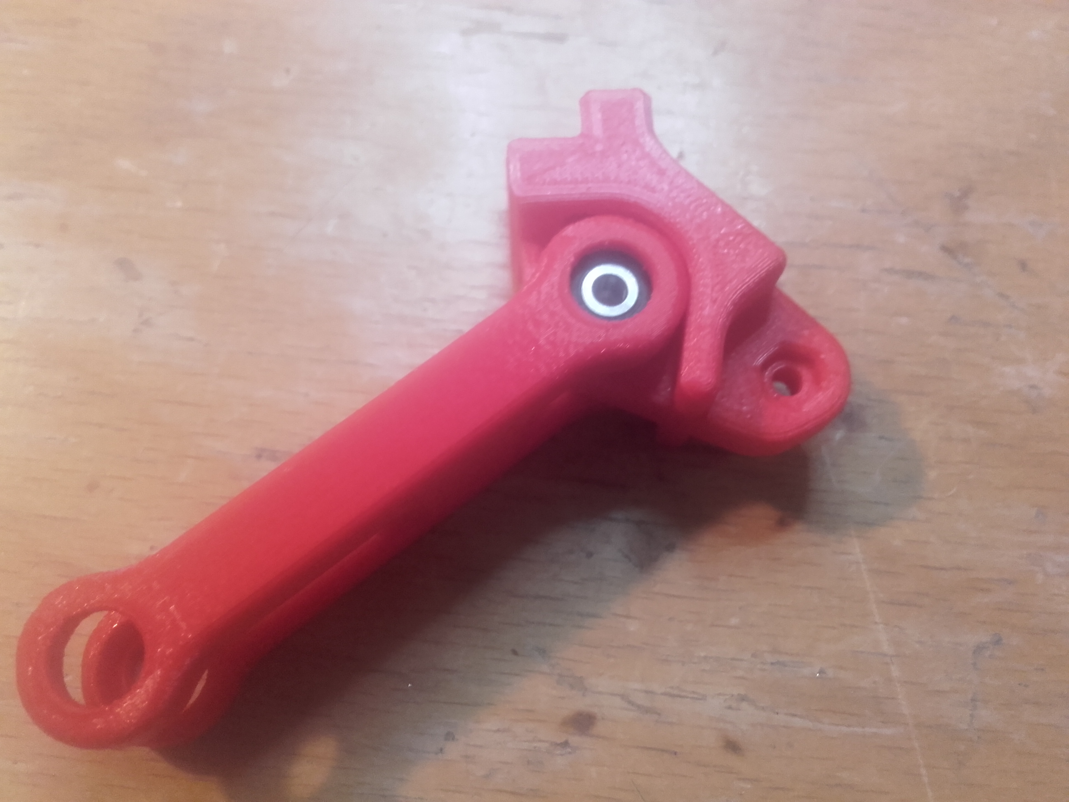
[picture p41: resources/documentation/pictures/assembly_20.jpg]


Fasten an M3x20mm screw in the pivot. Fasten on the other side an additional (optionally self-locking) M3 nut.

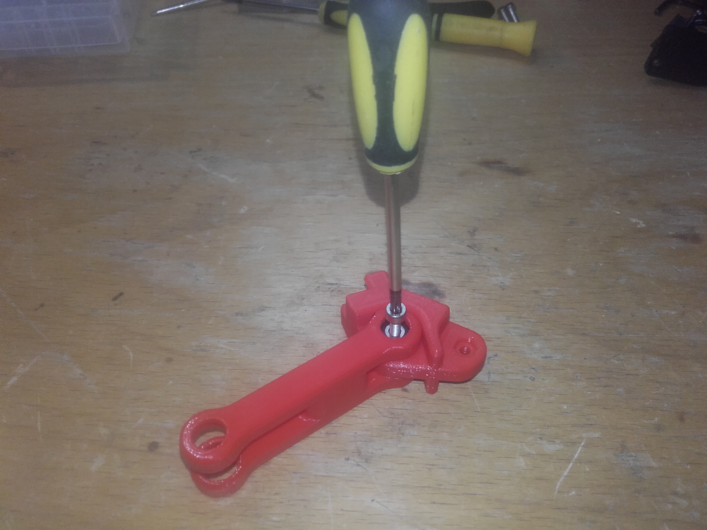
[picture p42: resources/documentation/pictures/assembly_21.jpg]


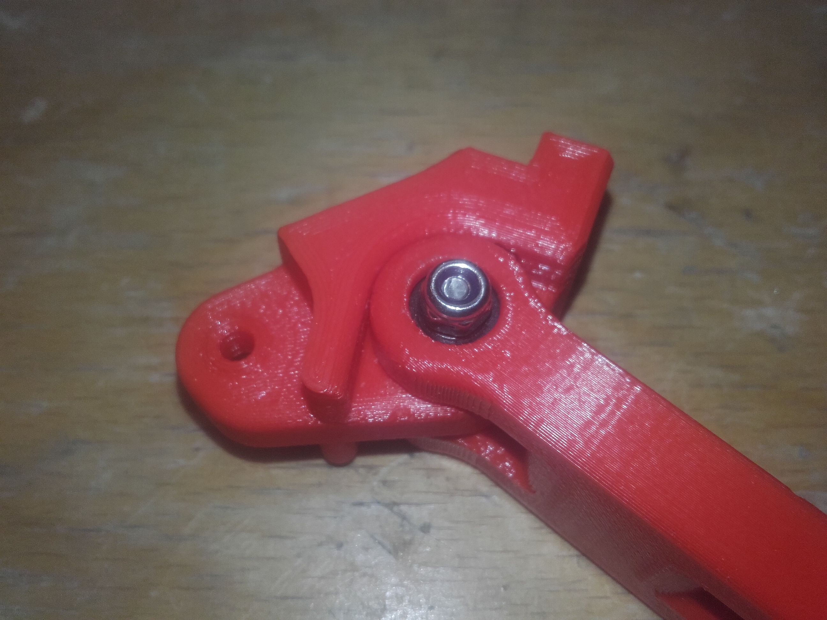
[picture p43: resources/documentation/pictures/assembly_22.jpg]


Repeat the procedures for all finger, screw the other end of the springs in place and voilà! The gripper is assembled. Please refer to the main readme for mounting on it on a HEBI actuator and changing the finger tips.

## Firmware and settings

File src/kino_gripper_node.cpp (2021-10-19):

#include <ros/ros.h>
#include <string>
#include <kino_gripper.h>
#include "control_msgs/GripperCommand.h"


class KinoGripperNode: public KinoGripper {
public:
	KinoGripperNode(char const* device_name);
private:
	void SetSubAndPub(ros::NodeHandle& private_nh);
	void GetParam(ros::NodeHandle& private_nh);
	void GripperCmdCallback(const control_msgs::GripperCommand& msg);

	virtual void PrintError(std::string& error_msg);
	virtual void PrintWarning(std::string& warning_msg);

	ros::Subscriber gripper_cmd_sub;

	const uint8_t default_device_id_ = 1;
	const int default_baudrate_ = 1000000;
};

KinoGripperNode::KinoGripperNode(char const* device_name = "/dev/ttyACM0") : KinoGripper(1, device_name, 1000000){
	ros::NodeHandle nh;
	ros::NodeHandle private_nh("~");

	GetParam(private_nh);
	InitGripper();				// To execute before setting up command subscriber
	SetSpeed(50);				// Set low speed
	SetSubAndPub(private_nh);
}

void KinoGripperNode::GetParam(ros::NodeHandle& private_nh){
	// Get baudrate
	if(!private_nh.getParam("baudrate", baudrate_)){
		baudrate_ = default_baudrate_;
		ROS_INFO_STREAM("Kino gripper: using default baudrate " << baudrate_ << "bps");
	}

	// Get Dynamixel servomotor device id
	if(!private_nh.getParam("device_id", device_id_)){
		device_id_ = default_device_id_;
		ROS_INFO_STREAM("Kino gripper: using default device id " << device_id_);
	}
}

void KinoGripperNode::SetSubAndPub(ros::NodeHandle& private_nh){
	gripper_cmd_sub = private_nh.subscribe("gripper_cmd", 1000, &KinoGripperNode::GripperCmdCallback, this);
}

void KinoGripperNode::GripperCmdCallback(const control_msgs::GripperCommand& msg){
	Close((msg.position)*1000); // Convert from message (m) to mm
	return;
}

void KinoGripperNode::PrintError(std::string& error_msg){
	ROS_ERROR_STREAM("Kino gripper node: " << error_msg);
}

void KinoGripperNode::PrintWarning(std::string& warning_msg){
	ROS_WARN_STREAM("Kino gripper node: " << warning_msg);
}


int main(int argc, char **argv){
	ros::init(argc, argv, "kino_gripper");
	ros::NodeHandle nh;
	ros::NodeHandle private_nh("~");


	std::string servo_port = "/dev/ttyACM0";	// Default servomotor port
	private_nh.getParam("port", servo_port);	// Try to get port param, use default if unsuccessful
	KinoGripperNode gripper_node(servo_port.c_str());	// Create gripper object

	while(ros::ok()){
		ros::spin();
	}

	ROS_INFO_STREAM("Kino gripper node: shutting down");

	return 0;
}

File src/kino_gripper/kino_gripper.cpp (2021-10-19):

#include "kino_gripper.h"

KinoGripper::KinoGripper(int device_id, char const* device_name, int baudrate) : device_id_(device_id), device_name_(device_name), baudrate_(baudrate){
}

void KinoGripper::InitGripper(){
	// Create Inverser Kinematics solver
	ik_solver_ = std::unique_ptr<GripperInverseKinematics>(new GripperInverseKinematics(min_angle_, max_angle_));

	// Create servomotor handler
	gripper_servo_ = std::unique_ptr<DynamixelAX12Handler>(new DynamixelAX12Handler(device_id_, device_name_, baudrate_));

	// Initalize servomotor
	gripper_servo_->InitServo();
}

bool KinoGripper::SetSpeed(uint16_t speed){
	speed_ = speed;
	return WriteSpeed();
}

bool KinoGripper::WriteSpeed(){
	try{
		gripper_servo_->SetSpeed(speed_);
	}
	catch (DynamixelAX12Exception& e){
		std::string error_msg = "could not set gripper speed, "+std::string(e.what());
		PrintWarning(error_msg);
		return false;
	}
	return true;
}

bool KinoGripper::EnableTorque(bool enable){
	try{
		gripper_servo_->EnableTorque(enable);
	}
	catch (DynamixelAX12Exception& e){
		std::string error_msg = "could not enable gripper torque, "+std::string(e.what());
		PrintWarning(error_msg);
		return false;
	}
	return true;
}

bool KinoGripper::SetMinMaxAngle(uint16_t min_angle, uint16_t max_angle){
	min_angle_ = min_angle;
	max_angle_ = max_angle;
	return WriteMinMaxAngle();
}

bool KinoGripper::WriteMinMaxAngle(){
	try{
		EnableTorque(false);
		gripper_servo_->SetMinMaxAngle(min_angle_, max_angle_);
	}
	catch (DynamixelAX12Exception& e){
		std::string error_msg = "could not set min-max angles, "+std::string(e.what());
		PrintWarning(error_msg);
		return false;
	}
	return true;	
}

bool KinoGripper::SetCompliance(uint8_t cw_margin, uint8_t ccw_margin, uint8_t cw_slope=32, uint8_t ccw_slope=32, uint16_t punch=32){
	cw_margin_ = cw_margin;
	ccw_margin_ = ccw_margin;
	cw_slope_ = cw_slope;
	ccw_slope_ = ccw_slope;
	punch_ = punch;
	return WriteCompliance();
}

bool KinoGripper::WriteCompliance(){
	try{
		EnableTorque(false);
		gripper_servo_->SetCompliance(cw_margin_, ccw_margin_, cw_slope_, ccw_slope_, punch_);
	}
	catch (DynamixelAX12Exception& e){
		std::string error_msg = "could not set gripper compliance values, "+std::string(e.what());
		PrintWarning(error_msg);
		return false;
	}
	return true;	
}

// Close to specified distance between fingers
bool KinoGripper::Close(float position){
	closing_angle_ = max(ik_solver_->GetStepsFromPosition(position),min_angle_);
	try{
		WriteSpeed();
		WriteCompliance();
		EnableTorque(true);
		gripper_servo_->SendPositionCommand(closing_angle_); // position in mm
	}
	catch (DynamixelAX12Exception& e){
		std::string error_msg = "could not close gripper, "+std::string(e.what());
		PrintWarning(error_msg);
		return false;
	}
	return true;
}

bool KinoGripper::Open(){
	try{
		WriteSpeed();
		WriteCompliance();
		EnableTorque(true);
		gripper_servo_->SendPositionCommand(max_angle_);
	}
	catch (DynamixelAX12Exception& e){
		std::string error_msg = "could not close gripper, "+std::string(e.what());
		PrintWarning(error_msg);
		return false;
	}
	return true;
}

bool KinoGripper::IsClosed() {
	try{
		// If gripper is not in movement and angle is close to goal, gripper is considered closed
		if (!IsMoving() && (abs(gripper_servo_->CurrPosition() - closing_angle_) <= angle_threshold_)) return true;
		else return false;
	}
	catch (DynamixelAX12Exception& e){
		std::string error_msg = "could not get gripper info, "+std::string(e.what());
		PrintWarning(error_msg);
		return false;
	}
}

bool KinoGripper::IsMoving() {
	try{
		return gripper_servo_->IsMoving();
	}
	catch (DynamixelAX12Exception& e){
		std::string error_msg = "could not get gripper info, "+std::string(e.what());
		PrintWarning(error_msg);
		return false;
	}
}

void KinoGripper::PrintError(std::string& error_msg){
	std::cerr << error_msg << std::endl;
}

void KinoGripper::PrintWarning(std::string& warning_msg){
	std::cerr << warning_msg << std::endl;
}

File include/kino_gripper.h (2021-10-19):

#ifndef KINO_GRIPPER_H
#define KINO_GRIPPER_H

#include <memory>
#include <limits>
#include <string>
#include <iostream>
#include "dynamixel_ax12_handler.h"
#include "gripper_inverse_kinematics.h"

/* Kino Gripper Class

Uses an interface to a Dynamixel AX12 servomotor
to control the gripper 
*/
class KinoGripper{
public:
	KinoGripper(int device_id, char const* device_name, int baudrate);
	void InitGripper();

	bool SetSpeed(uint16_t speed);
	bool SetMinMaxAngle(uint16_t min_angle, uint16_t max_angle);
	bool SetCompliance(uint8_t cw_margin, uint8_t ccw_margin, uint8_t cw_slope, uint8_t ccw_slope, uint16_t punch);
	bool Close(float distance);
	bool Open();
	bool IsClosed();
	bool IsMoving();

protected:
	std::unique_ptr<DynamixelAX12Handler> gripper_servo_;	// Servo handler pointer
	std::unique_ptr<GripperInverseKinematics> ik_solver_;	// Inverse Kinematics

	int device_id_;
	int baudrate_;
	char const* device_name_;

	bool EnableTorque(bool enable);
	virtual void PrintError(std::string& error_msg);
	virtual void PrintWarning(std::string& warning_msg);

	uint16_t min_angle_ = 392;		// Default value for minimum servomotor angle (closed gripper)
	uint16_t max_angle_ = 512;		// Default value for maximum servomotor angle (open gripper)
	uint16_t angle_threshold_ = 3; 	// Angle threshold to consider the gripper closed
	uint16_t speed_ = 50;
	uint8_t cw_margin_ = 1;
	uint8_t ccw_margin_ = 1;
	uint8_t cw_slope_ = 32;
	uint8_t ccw_slope_ = 32;
	uint16_t punch_ = 32;
	uint16_t closing_angle_;
	bool init_ = false; 			// intialization flag

	bool WriteSpeed();
	bool WriteMinMaxAngle();
	bool WriteCompliance();
};

#endif //KINO_GRIPPER_H

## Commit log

2021-10-05 Added gripper class as library
2021-10-06 Add detection of reset
    [dynamixel_ax12_handler.cpp, dynamixel_ax12_handler.h, kino_gripper.cpp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]
2021-10-12 Add gripper IK library
2021-10-12 Implements IK on closing gripper
2021-10-12 Fix bug on wrong value being defined as closing angle
    [gripper_inverse_kinematics.cpp, kino_gripper.cpp]
2021-10-19 Add servo port as ROS param
2021-10-25 Add gripper description
2021-10-26 Add CAD and STL files
    [AX-12A-01.SLDPRT, AX-12A-02.SLDPRT, AX-12A-03.SLDPRT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]
2021-10-26 Add gripper features
2021-10-26 Adjusted (reduced) adaptive block support
    [base_test.STL]
2021-10-27 Add pic and adjustments CAD
    [base.SLDPRT, base_attachement.SLDPRT]
2021-10-27 Add mounting pic
2021-10-27 Add mounting instructions
2021-10-27 Add first assembly steps
2021-10-27 Add assembly steps pictures
2021-10-27 Adjust wrong dimensions
    [base_attachement.SLDPRT, kino_gripper.SLDASM]
2021-10-28 Finish assembly instructions
2021-10-28 Add missing pictures for assembly instructions
